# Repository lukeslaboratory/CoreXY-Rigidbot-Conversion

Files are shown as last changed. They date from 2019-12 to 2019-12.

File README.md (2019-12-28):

# CoreXY-Rigidbot-Conversion

Alright, here it is. This is essentially V0.9 for this Kit, I've been using it quite successfully for the past 6 months and feel that its stable enough to do whatever you need it to do reliably. Should just need to print off 1x of more/less everything, except for the braces.

Logo Title Text 1

Logo Title Text 1

Logo Title Text 1

### Assembly Notes
You'll need M3, M4, and M5 Drills and Taps. 
I use Heat-Set inserts in the extruder carrier, should be sized appropriately for the inserts linked.

**I recommend printing from [High-Temp PLA](https://amzn.to/2ZtWItk) or other sturdy materials like ABS.

### Purchased parts 
*Amazon Links are affiliate - I may earn a commission if you purchase thru amazon. Zyltech has a few coupons out there that take 10-15% off, do a search before purchasing.*

623mm 2020 <https://amzn.to/2MC0iw7> (X Axis) - Or wherever else you feel like, Zyltech Stocks 10packs for ~60 or so

609mm Lin Rail MGN12 (X Axis) - China or Zyltech

468x2 Lin Rail MGN12 (Y Axis) - China or Zyltech

2x Pulley GT2 20T - <https://amzn.to/354wVJj>

2x Smooth Idler 6mm - <https://amzn.to/2F0bkqN>

6x Toothed Idler 6mm <https://amzn.to/2EZI83h> - Buy 2x

1x Hemera w/ Omnipack -  <https://amzn.to/358qoNX> - Buy Direct from E3D?

1x Bltouch - I use a clone, but Genuine is always better? <https://amzn.to/2F0hNlE>

5015 - <https://amzn.to/2ZsCG2k>

D2HW_C201H - Digikey or amazon - <https://amzn.to/355iODo>

Assorted M3 Screws <https://amzn.to/2ZFBkS5>

M3 Hammer Nuts <https://amzn.to/2SyZyfg>

Assorted M4 Screws - <https://amzn.to/2suLEQm>

M4 Heat-Set Inserts for Hemera - <https://amzn.to/2rzr29n>

Assorted m5 Screws - <https://amzn.to/2EZIDub>

#### Other Printed Kits I Use
[Hemera OmniPack](https://www.thingiverse.com/thing:4015118)
[MMU2 Filament Sensor](https://www.thingiverse.com/thing:4015190)

### CONFIGs
I currently run a Duet Wifi 2. Configs are Zipped.
<https://www.duet3d.com/DuetWifi> - Genuine
<http://www.zyltech.com/new-zyltech-duet-2-32-bit-board-with-7-touch-screen/> Clone with 7" Touchscreen - Zyltech.

Marlin Config is zipped as well. Likely needs a 32 bit board! 8bit boards can't run fast enough on most coreXY geometries. <https://amzn.to/39nbc2I> SKR1.3 with TMC Drivers should do nicely. 

*All of these files are for the Rigidbot Big with 0.9deg/step XY motors*
To convert this over to the regular rigidbot, it should work by shortening by 6" for X-axis Components and 2" for Y-Axis Components

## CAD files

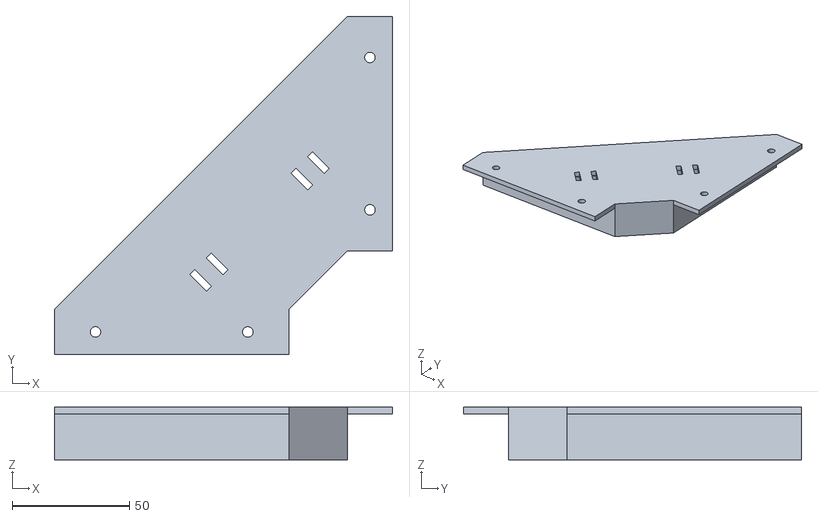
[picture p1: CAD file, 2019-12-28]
STL's/Generic Rigidbot Corner Brace v3.stl
144.2 x 144.2 x 22.5

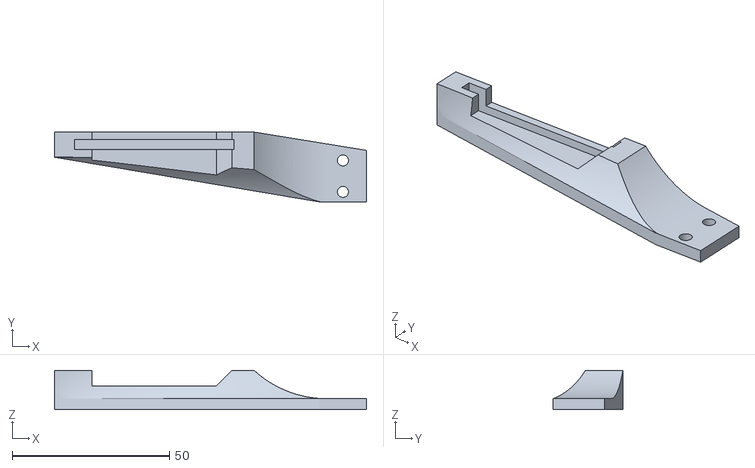
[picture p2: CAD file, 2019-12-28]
STL's/Wiper Mount v1.stl
99.3 x 22.2 x 12.5

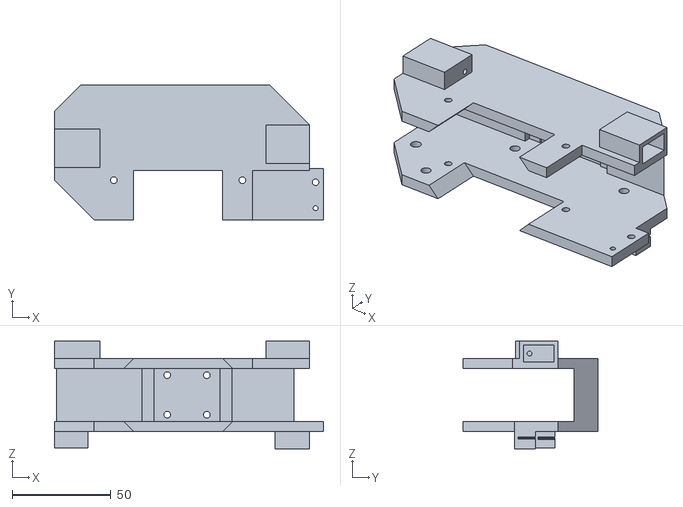
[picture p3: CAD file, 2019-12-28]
STL's/Hermes Plastic Carriage.stl
136.0 x 68.0 x 54.5

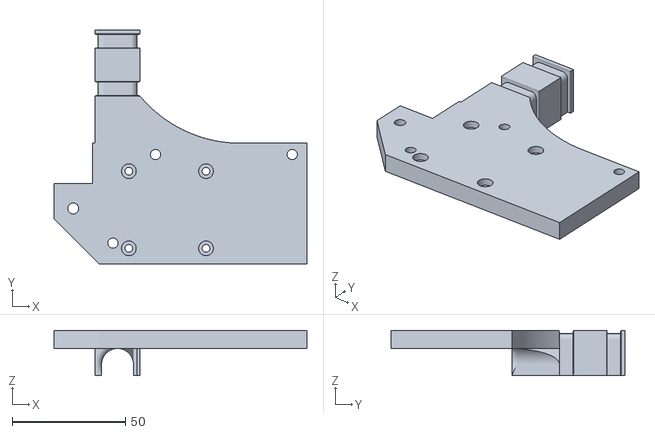
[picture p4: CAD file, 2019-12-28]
STL's/Hermes Tray.stl
111.5 x 103.3 x 20.0

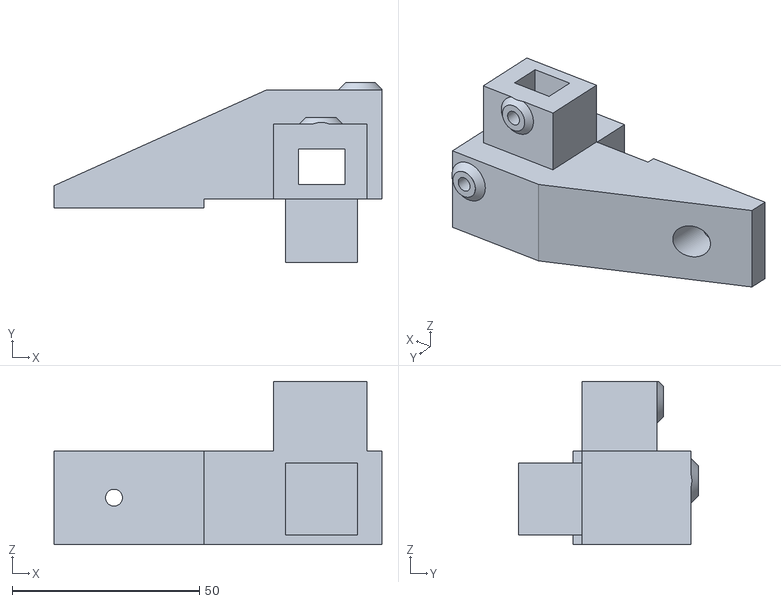
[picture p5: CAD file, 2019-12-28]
STL's/Belt Transfer Plastic.stl
87.5 x 48.0 x 43.5

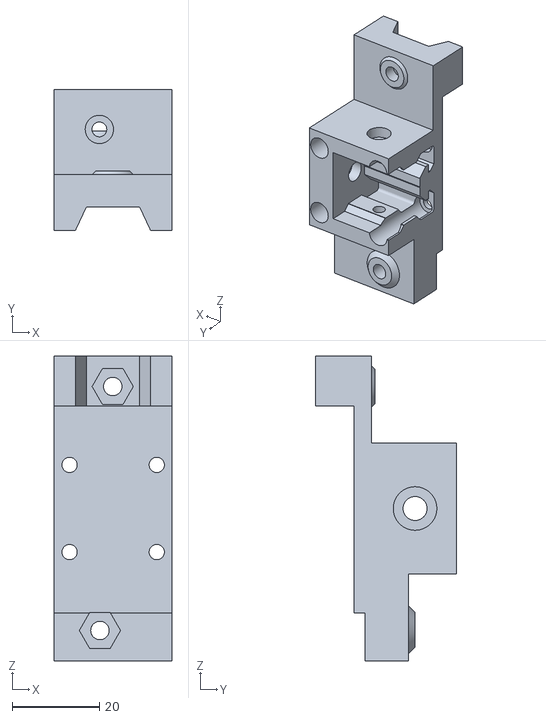
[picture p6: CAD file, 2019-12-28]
STL's/Y Mount Plastic(Mirror).stl
27.0 x 32.3 x 70.0

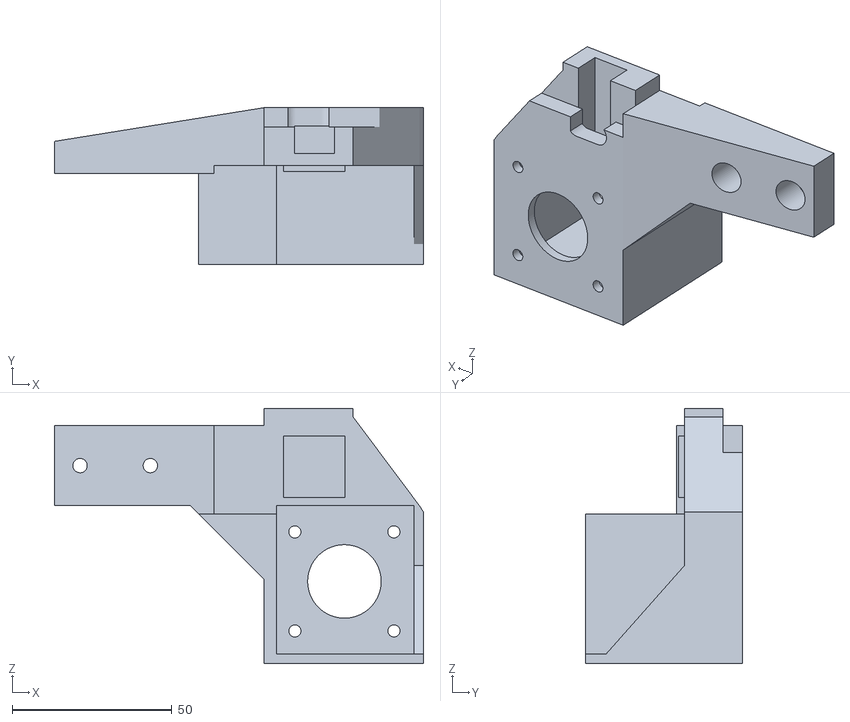
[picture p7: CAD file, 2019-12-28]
STL's/Plastic Motor Mount(Mirror).stl
115.5 x 49.0 x 79.9

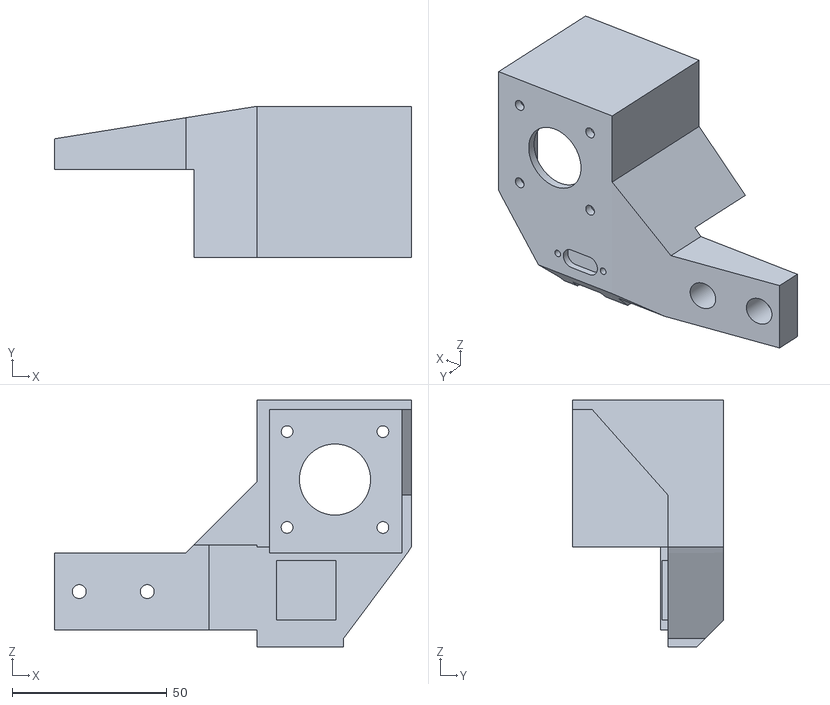
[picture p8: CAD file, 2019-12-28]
STL's/Plastic Motor Mount.stl
115.5 x 49.0 x 79.9

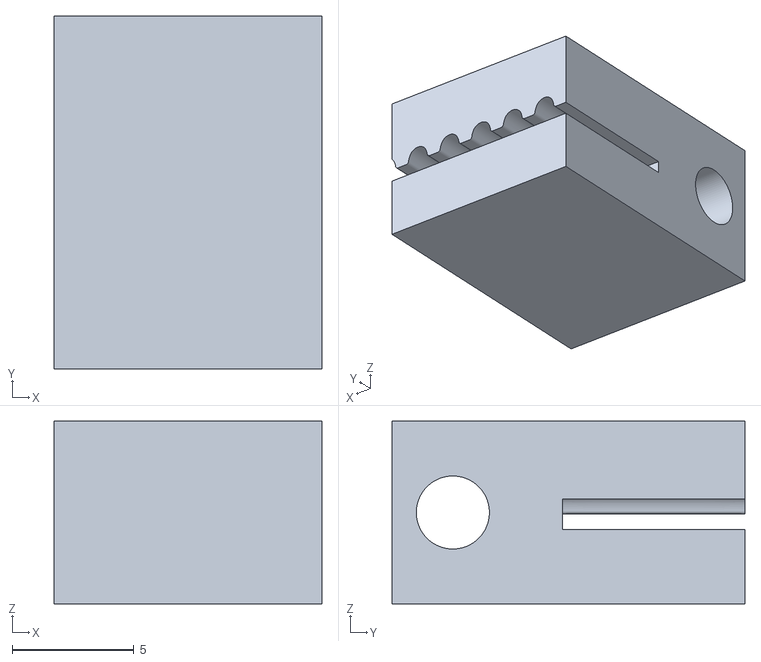
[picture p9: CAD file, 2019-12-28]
STL's/Timing Belt Holder v2.stl
11.0 x 14.5 x 7.50

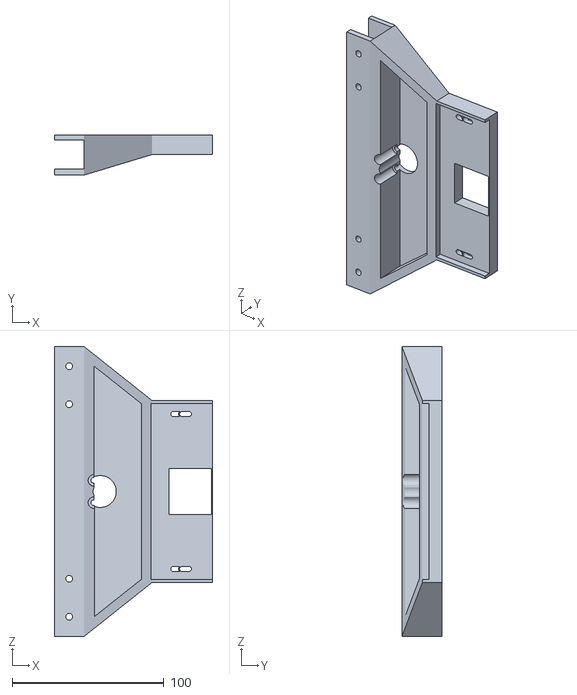
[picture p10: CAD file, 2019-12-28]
STL's/Z-Adapter Plate.stl
104.2 x 26.5 x 191.0

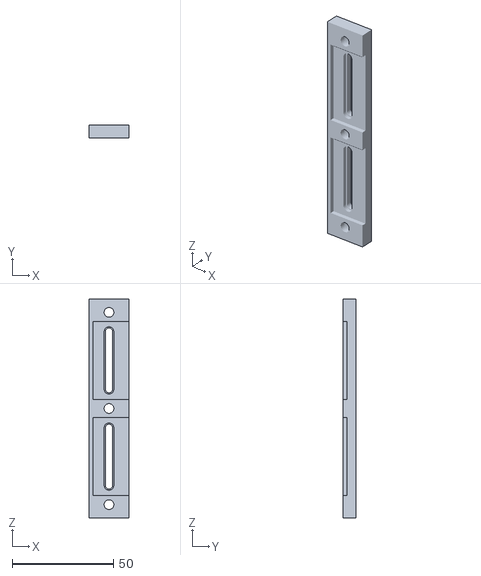
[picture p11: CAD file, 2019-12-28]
STL's/Long Support.stl
19.7 x 6.50 x 108.1

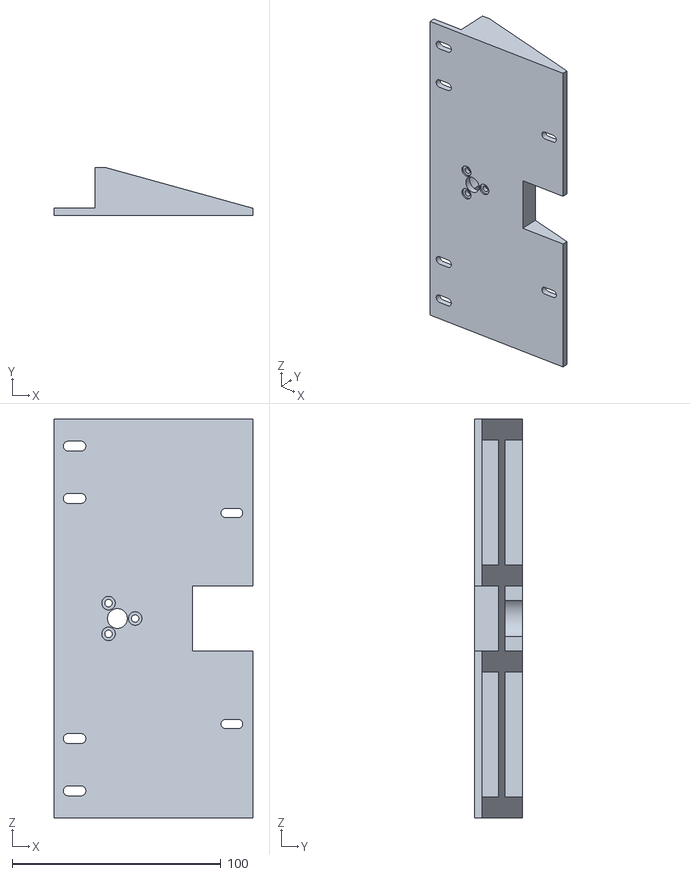
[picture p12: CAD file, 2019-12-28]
STL's/New Z Plate(Mirror).stl
95.0 x 23.0 x 191.0

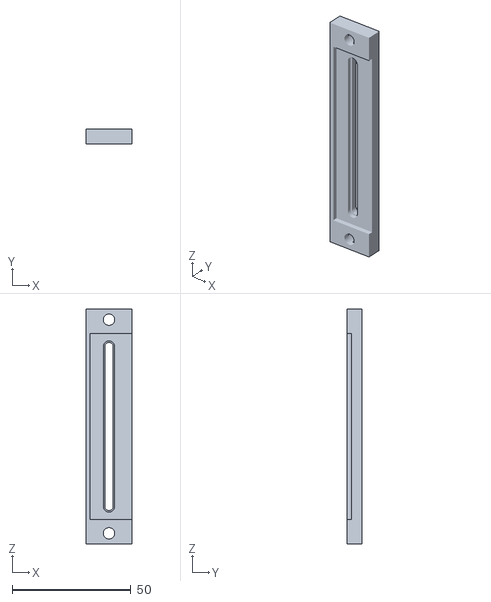
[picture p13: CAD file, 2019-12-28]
STL's/Mid Support.stl
19.5 x 6.50 x 99.0

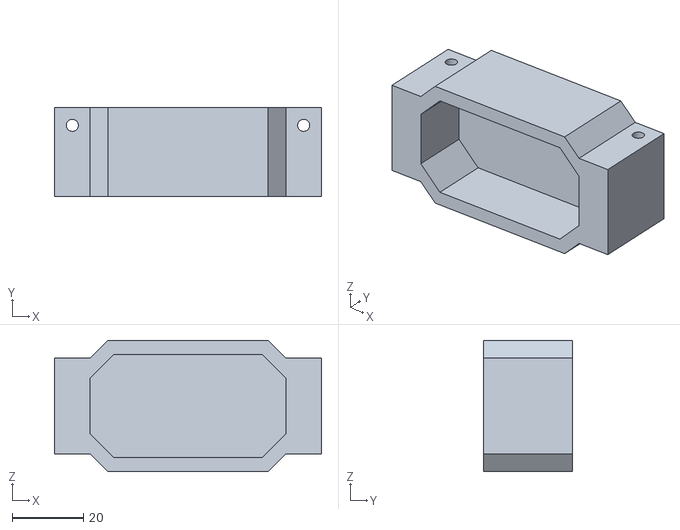
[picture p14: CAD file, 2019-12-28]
STL's/Hermes Underside.stl
75.0 x 25.0 x 36.9

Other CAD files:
STL's/Y Mount Plastic.stl
STL's/Belt Transfer Plastic(Mirror) (1).stl

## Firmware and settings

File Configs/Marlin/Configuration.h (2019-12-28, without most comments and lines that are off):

#pragma once
#define CONFIGURATION_H_VERSION 020000
#define STRING_CONFIG_H_AUTHOR "(Luke'sLab, Rigidbot XL Corexy)" // Who made the changes.
#define SHOW_BOOTSCREEN
#define STRING_SPLASH_LINE1 SHORT_BUILD_VERSION // will be shown during bootup in line 1
#define STRING_SPLASH_LINE2 "http://www.lukeslab.online"         // will be shown during bootup in line 2
#define SERIAL_PORT -1
#define BAUDRATE 250000
  #define MOTHERBOARD BOARD_AZTEEG_X5_GT
#define CUSTOM_MACHINE_NAME "MONGO"
#define EXTRUDERS 1
#define DEFAULT_NOMINAL_FILAMENT_DIA 1.75
#define TEMP_SENSOR_0 5
#define TEMP_SENSOR_1 0
#define TEMP_SENSOR_2 0
#define TEMP_SENSOR_3 0
#define TEMP_SENSOR_4 0
#define TEMP_SENSOR_5 0
#define TEMP_SENSOR_BED 1
#define TEMP_SENSOR_CHAMBER 0
#define DUMMY_THERMISTOR_998_VALUE 25
#define DUMMY_THERMISTOR_999_VALUE 100
#define MAX_REDUNDANT_TEMP_SENSOR_DIFF 10
#define TEMP_RESIDENCY_TIME     10  // (seconds) Time to wait for hotend to "settle" in M109
#define TEMP_WINDOW              1  // (°C) Temperature proximity for the "temperature reached" timer
#define TEMP_HYSTERESIS          3  // (°C) Temperature proximity considered "close enough" to the target
#define TEMP_BED_RESIDENCY_TIME 10  // (seconds) Time to wait for bed to "settle" in M190
#define TEMP_BED_WINDOW          1  // (°C) Temperature proximity for the "temperature reached" timer
#define TEMP_BED_HYSTERESIS      3  // (°C) Temperature proximity considered "close enough" to the target
#define HEATER_0_MINTEMP   5
#define HEATER_1_MINTEMP   5
#define HEATER_2_MINTEMP   5
#define HEATER_3_MINTEMP   5
#define HEATER_4_MINTEMP   5
#define HEATER_5_MINTEMP   5
#define BED_MINTEMP        5
#define HEATER_0_MAXTEMP 300
#define HEATER_1_MAXTEMP 275
#define HEATER_2_MAXTEMP 275
#define HEATER_3_MAXTEMP 275
#define HEATER_4_MAXTEMP 275
#define HEATER_5_MAXTEMP 275
#define BED_MAXTEMP      150
#define PIDTEMP
#define BANG_MAX 255     // Limits current to nozzle while in bang-bang mode; 255=full current
#define PID_MAX BANG_MAX // Limits current to nozzle while PID is active (see PID_FUNCTIONAL_RANGE below); 255=full current
#define PID_K1 0.95      // Smoothing factor within any PID loop
  #define PID_FUNCTIONAL_RANGE 10 // If the temperature difference between the target temperature and the actual temperature
  #define DEFAULT_Kp 9.
  #define DEFAULT_Ki .36
  #define DEFAULT_Kd 54
#define MAX_BED_POWER 255 // limits duty cycle to bed; 255=full current
#define EXTRUDE_MINTEMP 170
#define PREVENT_LENGTHY_EXTRUDE
#define EXTRUDE_MAXLENGTH 250
#define THERMAL_PROTECTION_HOTENDS // Enable thermal protection for all extruders
#define THERMAL_PROTECTION_BED     // Enable thermal protection for the heated bed
#define COREXY
#define USE_XMIN_PLUG
#define USE_ZMIN_PLUG
#define USE_YMAX_PLUG
#define USE_ZMAX_PLUG
#define ENDSTOPPULLUPS
#define X_MIN_ENDSTOP_INVERTING true // Set to true to invert the logic of the endstop.
#define Y_MIN_ENDSTOP_INVERTING true // Set to true to invert the logic of the endstop.
#define Z_MIN_ENDSTOP_INVERTING true // Set to true to invert the logic of the endstop.
#define X_MAX_ENDSTOP_INVERTING false // Set to true to invert the logic of the endstop.
#define Y_MAX_ENDSTOP_INVERTING true // Set to true to invert the logic of the endstop.
#define Z_MAX_ENDSTOP_INVERTING true // Set to true to invert the logic of the endstop.
#define Z_MIN_PROBE_ENDSTOP_INVERTING true // Set to true to invert the logic of the probe.
#define X_DRIVER_TYPE  TMC2660
#define Y_DRIVER_TYPE  TMC2660
#define Z_DRIVER_TYPE  TMC2660
#define E0_DRIVER_TYPE  TMC2660
#define DEFAULT_AXIS_STEPS_PER_UNIT   { 160, 160, 1600, 281.4 }
#define DEFAULT_MAX_FEEDRATE          { 700, 700, 10, 100 }
#define DEFAULT_MAX_ACCELERATION      { 3000, 3000, 100, 10000 }
#define DEFAULT_ACCELERATION          3000    // X, Y, Z and E acceleration for printing moves
#define DEFAULT_RETRACT_ACCELERATION  3000    // E acceleration for retracts
#define DEFAULT_TRAVEL_ACCELERATION   3000    // X, Y, Z acceleration for travel (non printing) moves
#define JUNCTION_DEVIATION
  #define JUNCTION_DEVIATION_MM .4*(10^2)/3000  // (mm) Distance from real junction edge, .4*jerk^2/accel
#define DEFAULT_EJERK    5.0  // May be used by Linear Advance
#define S_CURVE_ACCELERATION
#define Z_MIN_PROBE_PIN Z_MAX_PIN // Pin 32 is the RAMPS default
#define BLTOUCH
#define X_PROBE_OFFSET_FROM_EXTRUDER 35  // X offset: -left  +right  [of the nozzle]
#define Y_PROBE_OFFSET_FROM_EXTRUDER 19  // Y offset: -front +behind [the nozzle]
#define Z_PROBE_OFFSET_FROM_EXTRUDER -1.85   // Z offset: -below +above  [the nozzle]
#define MIN_PROBE_EDGE 10
#define XY_PROBE_SPEED 3600
#define Z_PROBE_SPEED_FAST HOMING_FEEDRATE_Z
#define Z_PROBE_SPEED_SLOW (Z_PROBE_SPEED_FAST / 2)
#define Z_CLEARANCE_DEPLOY_PROBE   15 // Z Clearance for Deploy/Stow
#define Z_CLEARANCE_BETWEEN_PROBES 15 // Z Clearance between probe points
#define Z_CLEARANCE_MULTI_PROBE     5 // Z Clearance between multiple probes
#define Z_PROBE_LOW_POINT          -2 // Farthest distance below the trigger-point to go before stopping
#define Z_PROBE_OFFSET_RANGE_MIN -20
#define Z_PROBE_OFFSET_RANGE_MAX 20
#define Z_MIN_PROBE_REPEATABILITY_TEST
#define X_ENABLE_ON 0
#define Y_ENABLE_ON 0
#define Z_ENABLE_ON 0
#define E_ENABLE_ON 0 // For all extruders
#define DISABLE_X false
#define DISABLE_Y false
#define DISABLE_Z false
#define DISABLE_E false             // For all extruders
#define DISABLE_INACTIVE_EXTRUDER   // Keep only the active extruder enabled
#define INVERT_X_DIR false
#define INVERT_Y_DIR false
#define INVERT_Z_DIR false
#define INVERT_E0_DIR false
#define INVERT_E1_DIR false
#define INVERT_E2_DIR false
#define INVERT_E3_DIR false
#define INVERT_E4_DIR false
#define INVERT_E5_DIR false
#define X_HOME_DIR -1
#define Y_HOME_DIR 1
#define Z_HOME_DIR -1
#define X_BED_SIZE 406
#define Y_BED_SIZE 300
#define X_MIN_POS -55
#define Y_MIN_POS 0
#define Z_MIN_POS 0
#define X_MAX_POS X_BED_SIZE
#define Y_MAX_POS Y_BED_SIZE
#define Z_MAX_POS 355
#define MIN_SOFTWARE_ENDSTOPS
  #define MIN_SOFTWARE_ENDSTOP_X
  #define MIN_SOFTWARE_ENDSTOP_Y
  #define MIN_SOFTWARE_ENDSTOP_Z
#define MAX_SOFTWARE_ENDSTOPS
  #define MAX_SOFTWARE_ENDSTOP_X
  #define MAX_SOFTWARE_ENDSTOP_Y
  #define MAX_SOFTWARE_ENDSTOP_Z
#define AUTO_BED_LEVELING_UBL
#define RESTORE_LEVELING_AFTER_G28
  #define ENABLE_LEVELING_FADE_HEIGHT
  #define SEGMENT_LEVELED_MOVES
  #define LEVELED_SEGMENT_LENGTH 5.0 // (mm) Length of all segments (except the last one)
  #define G26_MESH_VALIDATION
    #define MESH_TEST_NOZZLE_SIZE    0.4  // (mm) Diameter of primary nozzle.
    #define MESH_TEST_LAYER_HEIGHT   0.2  // (mm) Default layer height for the G26 Mesh Validation Tool.
    #define MESH_TEST_HOTEND_TEMP  210    // (°C) Default nozzle temperature for the G26 Mesh Validation Tool.
    #define MESH_TEST_BED_TEMP      60    // (°C) Default bed temperature for the G26 Mesh Validation Tool.
    #define G26_XY_FEEDRATE         60    // (mm/s) Feedrate for XY Moves for the G26 Mesh Validation Tool.
  #define MESH_INSET 10              // Set Mesh bounds as an inset region of the bed
  #define GRID_MAX_POINTS_X 7      // Don't use more than 15 points per axis, implementation limited.
  #define GRID_MAX_POINTS_Y 7
  #define UBL_MESH_EDIT_MOVES_Z     // Sophisticated users prefer no movement of nozzle
  #define UBL_SAVE_ACTIVE_ON_M500   // Save the currently active mesh in the current slot on M500
#define LCD_BED_LEVELING
  #define MESH_EDIT_Z_STEP  0.025 // (mm) Step size while manually probing Z axis.
  #define LCD_PROBE_Z_RANGE 4     // (mm) Z Range centered on Z_MIN_POS for LCD Z adjustment
#define LEVEL_BED_CORNERS
  #define LEVEL_CORNERS_INSET 30    // (mm) An inset for corner leveling
  #define LEVEL_CORNERS_Z_HOP  4.0  // (mm) Move nozzle up before moving between corners
  #define LEVEL_CORNERS_HEIGHT 0.0  // (mm) Z height of nozzle at leveling points
#define HOMING_FEEDRATE_XY (50*60)
#define HOMING_FEEDRATE_Z  (8*60)
#define VALIDATE_HOMING_ENDSTOPS
#define EEPROM_SETTINGS     // Persistent storage with M500 and M501
#define EEPROM_CHITCHAT       // Give feedback on EEPROM commands. Disable to save PROGMEM.
#define HOST_KEEPALIVE_FEATURE        // Disable this if your host doesn't like keepalive messages
#define DEFAULT_KEEPALIVE_INTERVAL 2  // Number of seconds between "busy" messages. Set with M113.
#define BUSY_WHILE_HEATING            // Some hosts require "busy" messages even during heating
#define PREHEAT_1_LABEL       "PLA"
#define PREHEAT_1_TEMP_HOTEND 210
#define PREHEAT_1_TEMP_BED     60
#define PREHEAT_1_FAN_SPEED     0 // Value from 0 to 255
#define PREHEAT_2_LABEL       "ABS"
#define PREHEAT_2_TEMP_HOTEND 280
#define PREHEAT_2_TEMP_BED    110
#define PREHEAT_2_FAN_SPEED     0 // Value from 0 to 255
#define NOZZLE_PARK_FEATURE
  #define NOZZLE_PARK_POINT { (X_MIN_POS + 10), (Y_MAX_POS - 10), 20 }
  #define NOZZLE_PARK_XY_FEEDRATE 100   // (mm/s) X and Y axes feedrate (also used for delta Z axis)
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

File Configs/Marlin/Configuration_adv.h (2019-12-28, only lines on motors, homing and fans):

#define E0_AUTO_FAN_PIN FAN1_PIN
#define E1_AUTO_FAN_PIN -1
#define E2_AUTO_FAN_PIN -1
#define E3_AUTO_FAN_PIN -1
#define E4_AUTO_FAN_PIN -1
#define E5_AUTO_FAN_PIN -1
#define CHAMBER_AUTO_FAN_PIN -1
#define X_HOME_BUMP_MM 5
#define Y_HOME_BUMP_MM 5
#define Z_HOME_BUMP_MM 2
#define HOMING_BUMP_DIVISOR { 2, 2, 4 }  // Re-Bump Speed Divisor (Divides the Homing Feedrate)
#define HOME_Y_BEFORE_X
#define MICROSTEP_MODES { 16, 16, 16, 16, 16, 16 } // [1,2,4,8,16]
#define DIGIPOT_I2C_MOTOR_CURRENTS { 1.0, 1.0, 1.0, 1.0, 1.0, 1.0, 1.0, 1.0 }  //  AZTEEG_X3_PRO
#define LIN_ADVANCE
  #define LIN_ADVANCE_K .2    // Unit: mm compression per 1mm/s extruder speed
#define ADVANCED_PAUSE_FEATURE
  #define ADVANCED_PAUSE_PURGE_FEEDRATE        3  // (mm/s) Extrude feedrate (after loading). Should be slower than load feedrate.
  #define ADVANCED_PAUSE_PURGE_LENGTH         50  // (mm) Length to extrude after loading.
  #define ADVANCED_PAUSE_RESUME_PRIME          0  // (mm) Extra distance to prime nozzle after returning from park.
    #define X_CURRENT     1400  // (mA) RMS current. Multiply by 1.414 for peak current.
    #define X_MICROSTEPS   16  // 0..256
    #define Y_CURRENT     1400
    #define Y_MICROSTEPS   16
    #define Z_CURRENT     1700
    #define Z_MICROSTEPS   16
    #define E0_CURRENT    1000
    #define E0_MICROSTEPS  16
    #define CURRENT_STEP_DOWN     50  // [mA]
    #define REPORT_CURRENT_CHANGE
  #define X_HYBRID_THRESHOLD     100  // [mm/s]
  #define X2_HYBRID_THRESHOLD    100
  #define Y_HYBRID_THRESHOLD     100
  #define Y2_HYBRID_THRESHOLD    100
  #define Z_HYBRID_THRESHOLD       3
  #define Z2_HYBRID_THRESHOLD      3
  #define Z3_HYBRID_THRESHOLD      3
  #define E0_HYBRID_THRESHOLD     30
  #define E1_HYBRID_THRESHOLD     30
  #define E2_HYBRID_THRESHOLD     30
  #define E3_HYBRID_THRESHOLD     30
  #define E4_HYBRID_THRESHOLD     30
  #define E5_HYBRID_THRESHOLD     30

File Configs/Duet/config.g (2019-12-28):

; Configuration file for Duet 3 (firmware version 3)
; executed by the firmware on start-up
;
; generated by RepRapFirmware Configuration Tool v2.1.4 on Thu Dec 26 2019 17:05:21 GMT-0600 (Central Standard Time)

; General preferences
G90                                          ; send absolute coordinates...
M83                                          ; ...but relative extruder moves
M550 P"StableBot"                               ; set printer name

M667 S1                                      ; select CoreXY mode

; Drives
M569 P0.1 S1                                 ; physical drive 0.1 goes forwards
M569 P0.0 S1                                 ; physical drive 0.0 goes forwards
M569 P0.2 S1                                 ; physical drive 0.2 goes forwards
M569 P0.3 S1				                          ; physical drive 0.3 goes backwards
M569 P0.4 S1				                          ; physical drive 0.4 goes backwards
M569 P0.5 S0                                 ; physical drive 0.5 goes backwards
M584 X0.1 Y0.0 Z0.3:4:5 E0.2                     ; set drive mapping
M350 X16 Y16 Z16 E16 I1                      ; configure microstepping with interpolation
M92 X160.00 Y160.00 Z1600.00 E409.00         ; set steps per mm
M566 X900.00 Y900.00 Z12.00 E120.00          ; set maximum instantaneous speed changes (mm/min)
M203 X18000.00 Y18000.00 Z300.00 E3000.00    ; set maximum speeds (mm/min)
M201 X1000.00 Y1000.00 Z20.00 E250.00        ; set accelerations (mm/s^2)
M906 X1800 Y1800 Z1800 E1100 I30             ; set motor currents (mA) and motor idle factor in per cent
M84 S30                                      ; Set idle timeout

; Axis Limits
M208 X0 Y0 Z0 S1                             ; set axis minima
M208 X622 Y622 Z950 S0                       ; set axis maxima
M671 X311:-44.45:666.45 Y-57.15:164.8:164.8 S1 ; leadscrews at rear middle, front left+right

; Endstops
M574 X1 S0 P"io2.in"                         ; configure active-low endstop for low end on X via pin io2.in
M574 Y1 S0 P"io0.in"                         ; configure active-low endstop for low end on Y via pin io0.in
;M574 Y2 S0 P"io1.in"			                   ; configure active-low endstop for high end on Y via pin io1.in
M574 Z1 S2                                   ; configure Z-probe endstop for low end on Z

; Z-Probe
M950 S0 C"io8.out"                           ; create servo pin 0 for BLTouch
M558 P9 C"io8.in" H5 F120 T3600      ; set Z probe type to bltouch and the dive height + speeds
M558 H30                                     ;*** Remove this line after delta calibration has been done and new delta parameters have been saved
G31 P500 X-5 Y48 Z2.6                        ; set Z probe trigger value, offset and trigger height
M557 X15:600 Y15:600 S30                     ; define mesh grid

; Heaters
M308 S0 P"temp0" Y"thermistor" T100000 B4138 ; configure sensor 0 as thermistor on pin temp0
M950 H0 C"out1" T0                           ; create bed heater output on out1 and map it to sensor 0
M143 H0 S120                                 ; set temperature limit for heater 0 to 120C
M307 H0 B0 S0.66                             ; disable bang-bang mode for the bed heater and set PWM limit
M140 H0                                      ; map heated bed to heater 0
M308 S1 P"temp2" Y"thermistor" T100000 B4138 ; configure sensor 1 as thermistor on pin temp2
M950 H1 C"out2" T1                           ; create nozzle heater output on out2 and map it to sensor 1
M143 H1 S280                                 ; set temperature limit for heater 1 to 280C
M307 H1 B0 S1.00                             ; disable bang-bang mode for the nozzle heater and set PWM limit

; Fans
M950 F0 C"out7" Q500                         ; create fan 0 on pin out7 and set its frequency
M106 P0 S0 H-1                               ; set fan 0 value. Thermostatic control is turned off
M950 F1 C"out8" Q500                         ; create fan 1 on pin out8 and set its frequency
M106 P1 S1 H1 T45                            ; set fan 1 value. Thermostatic control is turned on

; Tools
M563 P0 D0 H1 F0                             ; define tool 0
G10 P0 X0 Y0 Z0                              ; set tool 0 axis offsets
G10 P0 R0 S0                                 ; set initial tool 0 active and standby temperatures to 0C

; Custom settings are not defined

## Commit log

2019-12-28 Initial Add Of Files
    [Belt Transfer Plastic(Mirror) (1).stl, Belt Transfer Plastic.stl, Hermes Plastic Carriage.stl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]
2019-12-28 Added Wiper Mount
    [Wiper Mount v1.stl]
2019-12-28 Added Marlin Configs
    [Configuration.h, Configuration_adv.h]

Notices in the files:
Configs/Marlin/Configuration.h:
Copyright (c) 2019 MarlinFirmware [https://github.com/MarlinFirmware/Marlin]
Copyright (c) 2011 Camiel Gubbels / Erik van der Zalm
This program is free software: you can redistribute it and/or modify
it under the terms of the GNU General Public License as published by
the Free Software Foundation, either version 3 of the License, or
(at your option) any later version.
